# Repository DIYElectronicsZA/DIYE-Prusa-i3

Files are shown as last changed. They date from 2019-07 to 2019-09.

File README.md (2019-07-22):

# DIYE-Prusa-i3
DIYElectronics version of the Prusa i3 https://diyelectronics.co.za

Based on the Original Prusa i3, the DIYElectronics Prusa i3 is a 3D printer project maintained by DIYElectronics.co.za
Originates in RepRap project.

This repository contains files and STLs of the printed parts.

**Links**

 * DIYElectronics website : http://diyelectronics.co.za
 * Product page : https://www.diyelectronics.co.za/store/printers/903-diyelectronics-prusa-i3-premium-kit.html
 * Build manual : https://www.diyelectronics.co.za/wiki/#3DPrinters/DIYPrinters/builddocprem/
 * Firmware : https://www.diyelectronics.co.za/firmware/

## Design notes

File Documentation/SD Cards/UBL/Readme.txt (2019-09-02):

On this SD Card, you will find "UBL.gcode"
This gcode script is used to initiate a UBL sequence.
You should run this script every time you:
	- Move / transport the printer
	- Remove / re-level the bed
	- If your bed has become warped over time

Read more about UBL at http://marlinfw.org/docs/features/unified_bed_leveling.html

If you have any queries, don't hesitate to contact Support@DIYElectronics.co.za

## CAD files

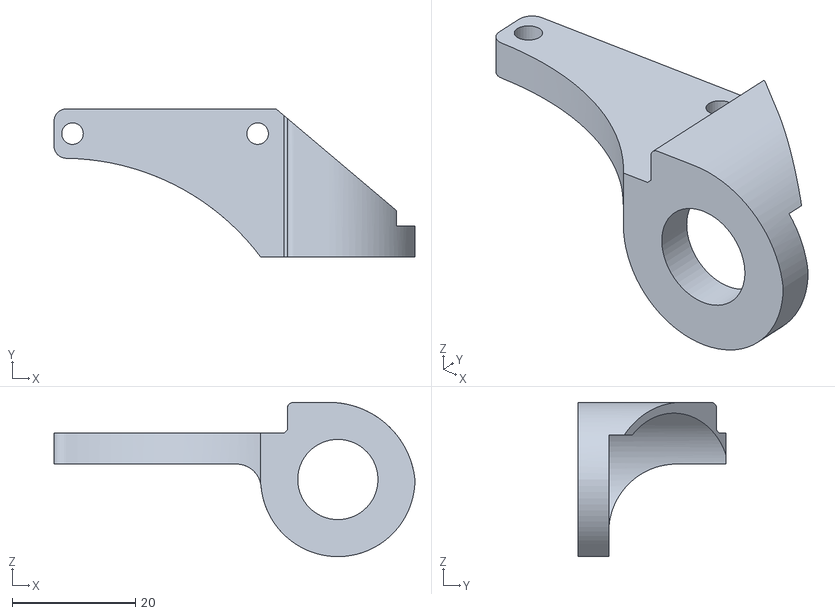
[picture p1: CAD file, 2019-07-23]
Printed Parts/Auto Level Kit/Autolevelmount.stl
58.5 x 24.0 x 25.0

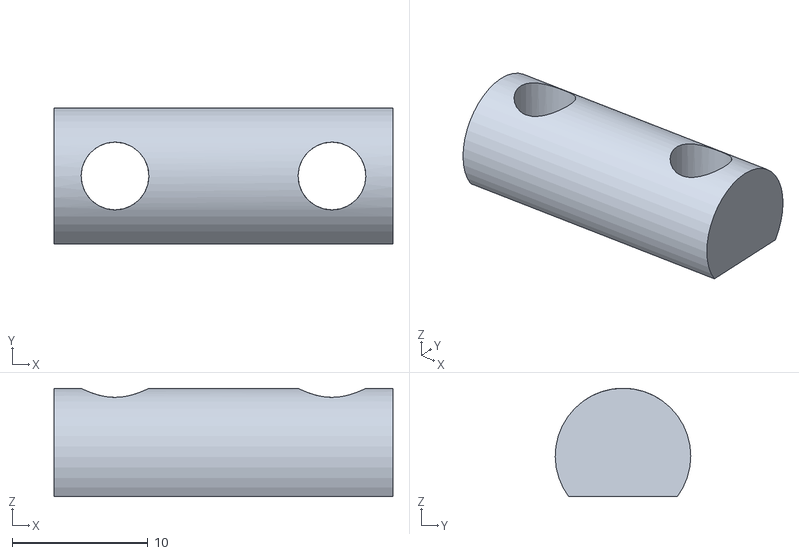
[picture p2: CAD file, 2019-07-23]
Printed Parts/Charlstruder/Birdnose Shaft/Birdnose shaft.stl
25.0 x 10.00 x 8.00

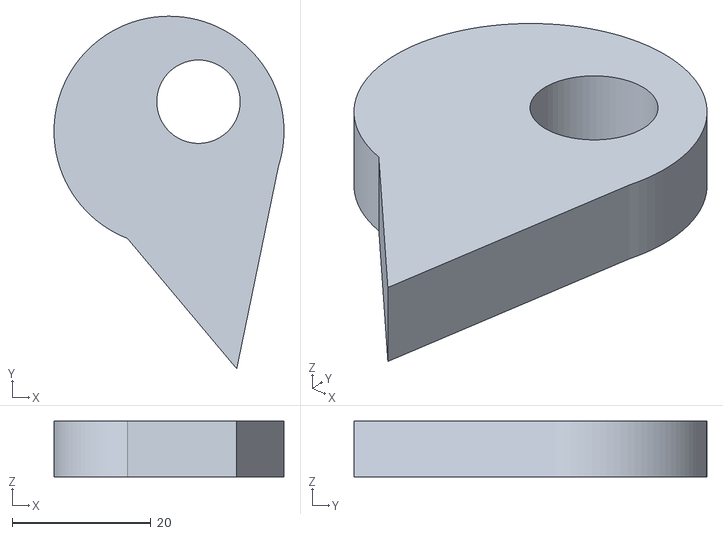
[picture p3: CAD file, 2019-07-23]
Printed Parts/Charlstruder/Birdnose/Birdnose.stl
33.1 x 50.7 x 8.00

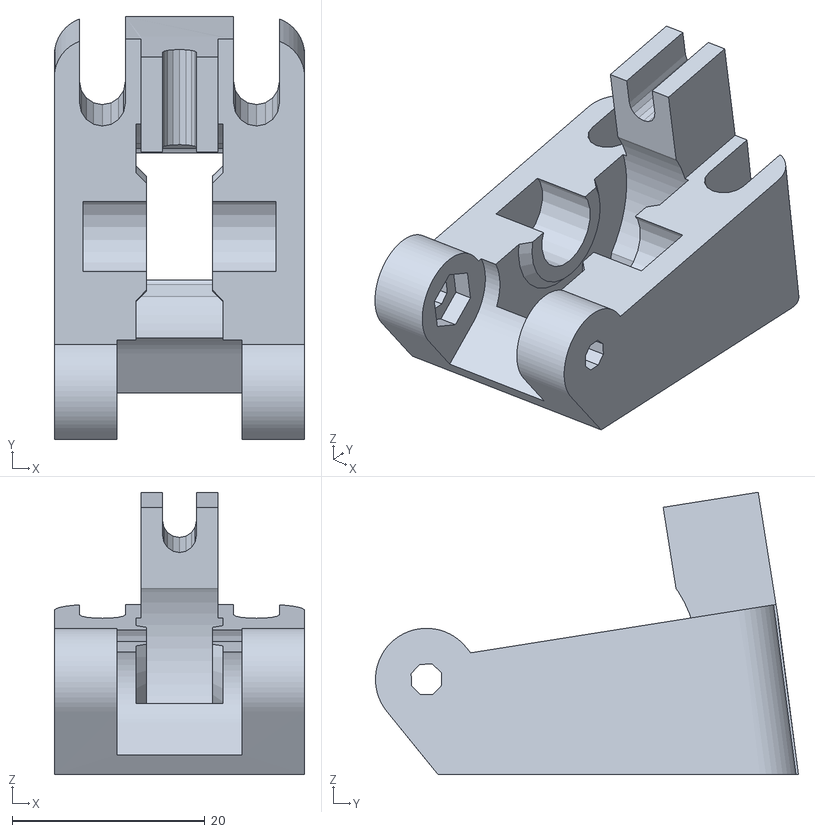
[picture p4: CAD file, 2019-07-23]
Printed Parts/Charlstruder/Charlstruder Birdnose Guidler/Birdnose Guidler.stl
26.0 x 43.9 x 29.3

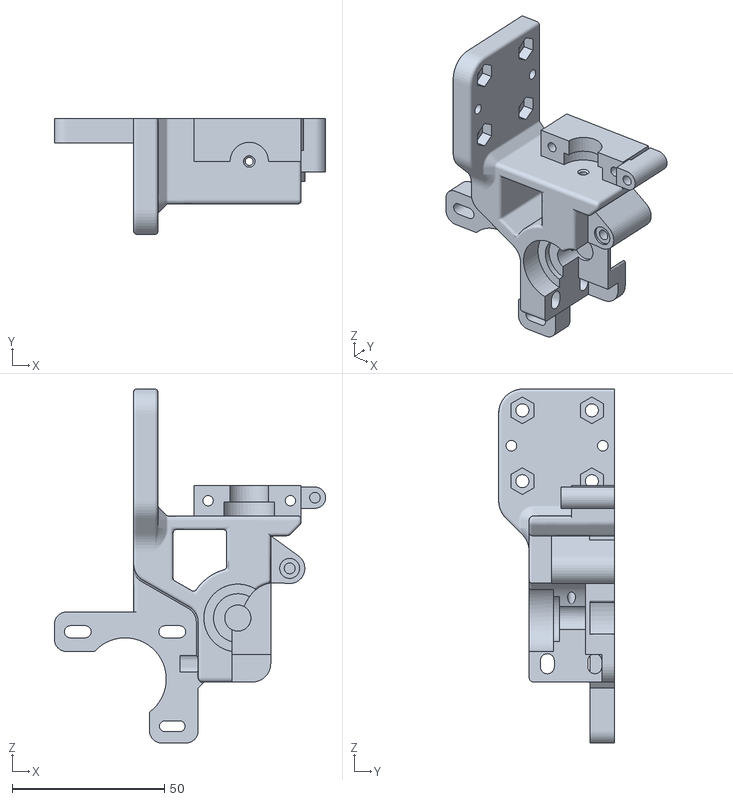
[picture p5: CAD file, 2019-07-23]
Printed Parts/Charlstruder/CharlStruder Body/Charlstruder_E3D_1.75mm_v1.1.stl
89.0 x 38.0 x 116.2

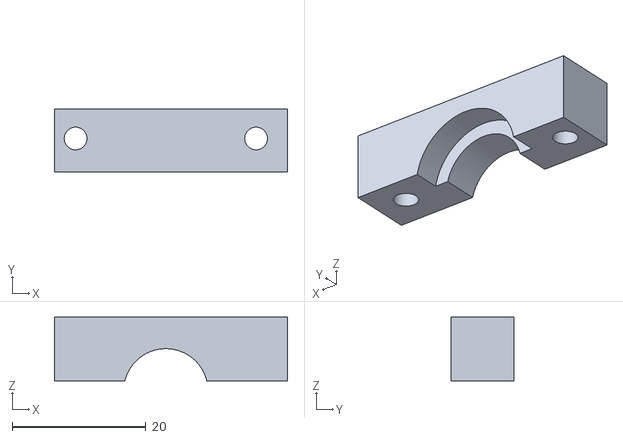
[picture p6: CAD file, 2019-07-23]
Printed Parts/Charlstruder/Charlstruder Collar/Hotend Collar.stl
34.9 x 9.40 x 9.50

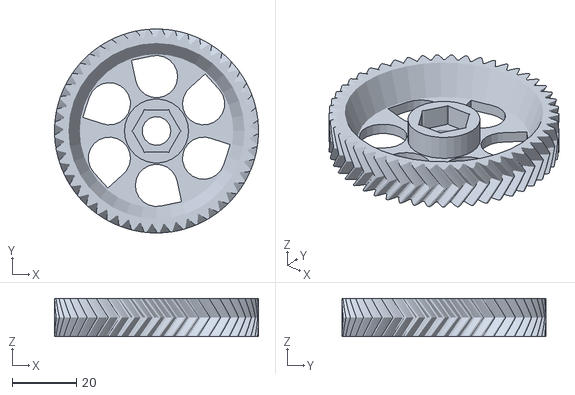
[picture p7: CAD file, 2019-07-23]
Printed Parts/Charlstruder/Charlstruder Gears/13mm Drive Gear/Charlstruder Gears.stl
63.7 x 63.7 x 12.0

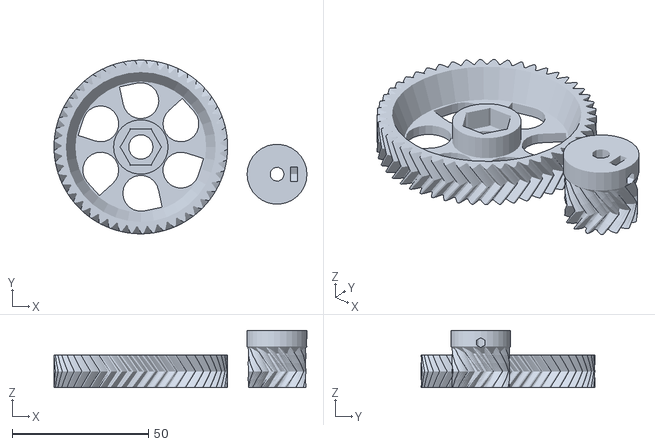
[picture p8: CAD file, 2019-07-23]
Printed Parts/Charlstruder/Charlstruder Gears/Pinion Gear/Charlstruder Gears.stl
92.9 x 63.7 x 21.0

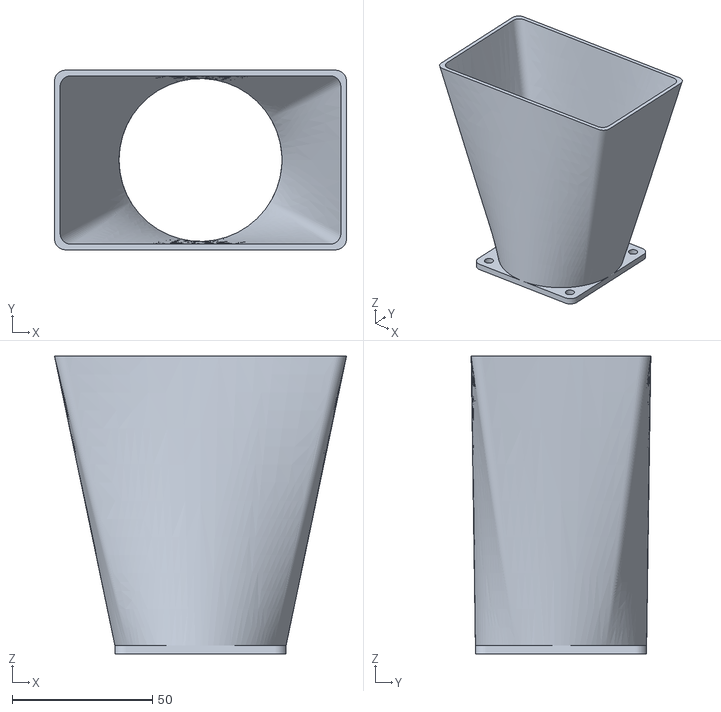
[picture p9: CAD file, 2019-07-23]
Printed Parts/DIY Enclosure/60mm Fan Duct/RampsFanExtenderShroud.STL
104.0 x 64.0 x 106.0

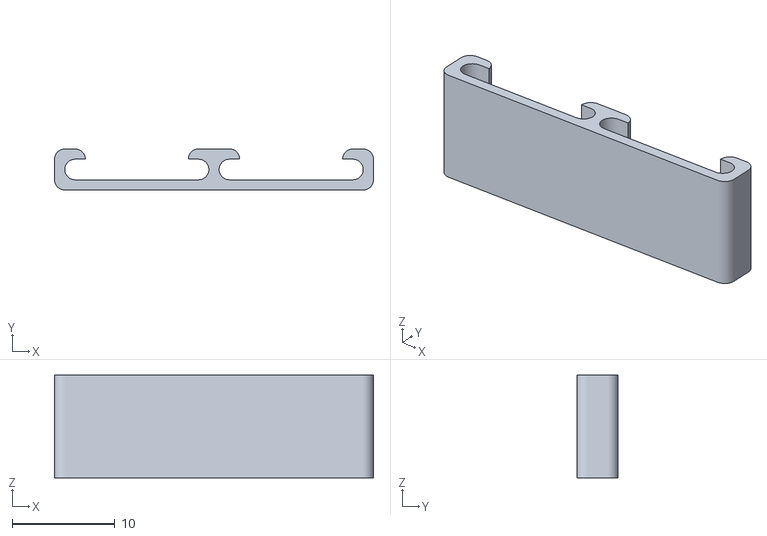
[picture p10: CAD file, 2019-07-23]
Printed Parts/DIY Enclosure/Cable Clip/Cable Clip.STL
31.0 x 4.00 x 10.0

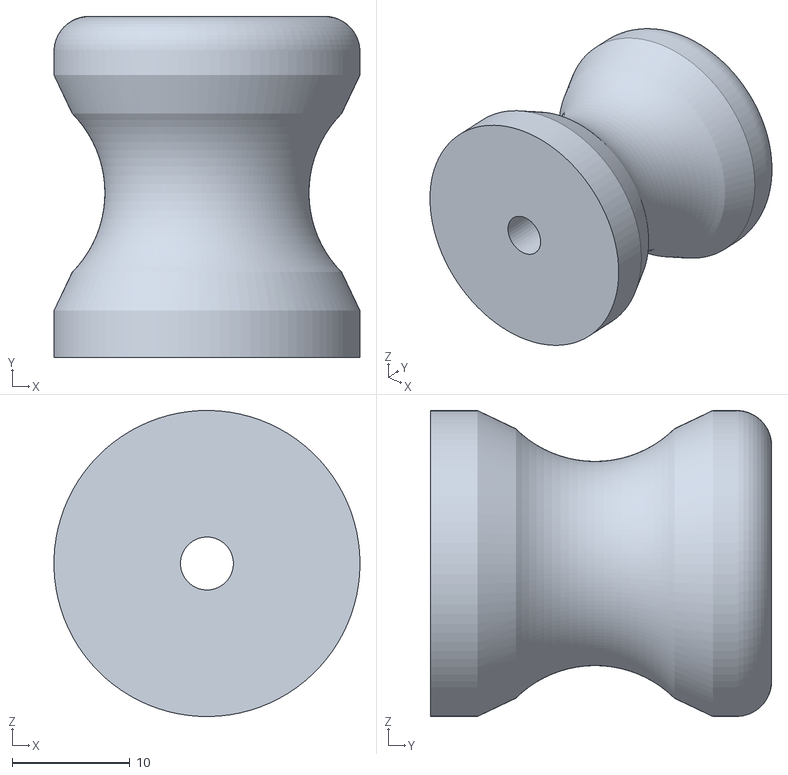
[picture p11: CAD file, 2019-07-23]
Printed Parts/DIY Enclosure/Door Knob/knob.stl
26.0 x 29.0 x 26.0

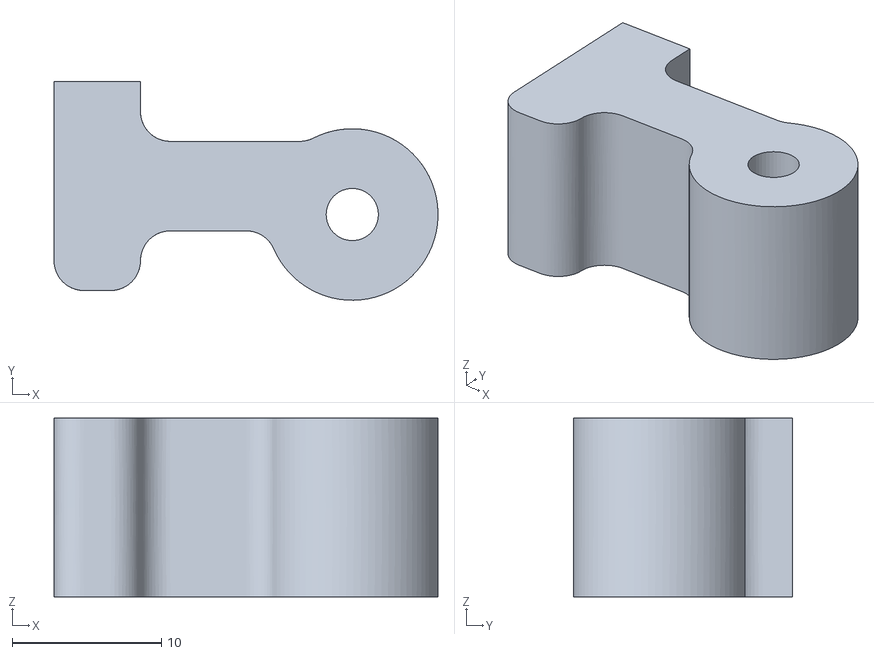
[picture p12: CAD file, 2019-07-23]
Printed Parts/DIY Enclosure/Door Magnet Mounts/frame mag latch.stl
25.7 x 14.7 x 12.0

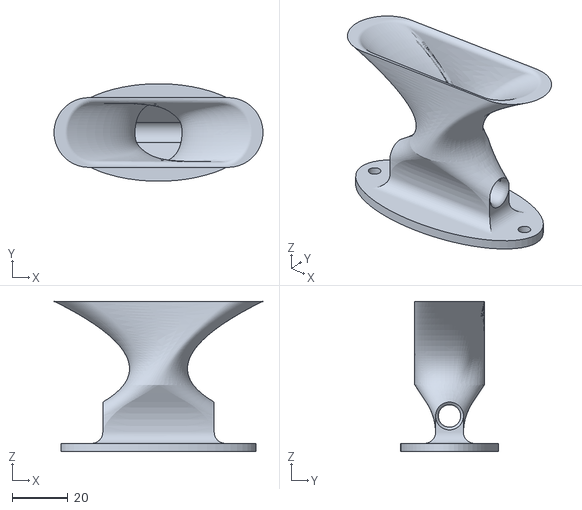
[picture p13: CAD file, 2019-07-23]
Printed Parts/DIY Enclosure/Filament Guides/Filament Guide 2.STL
75.0 x 35.0 x 54.0

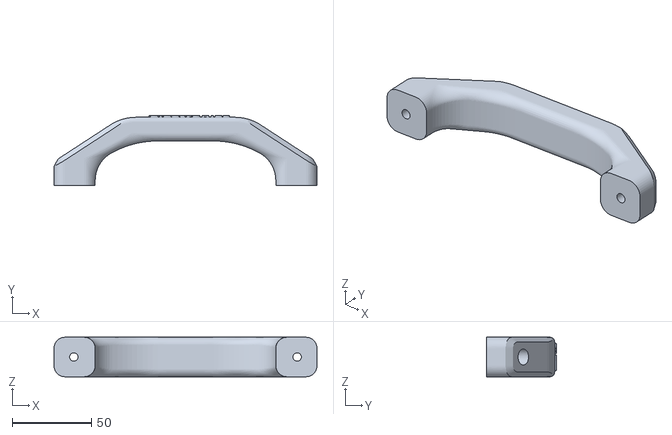
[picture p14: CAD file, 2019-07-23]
Printed Parts/DIY Enclosure/Handle/HandleV2.stl
166.0 x 44.0 x 25.0

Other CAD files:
Printed Parts/Charlstruder/Charlstruder Gears/14mm Drive Gear/Charlstruder Gear 14mm.stl
Printed Parts/DIY Enclosure/Hinge/hinge1.stl
Printed Parts/DIY Enclosure/Printer Mount/Prusa Mount.stl
Printed Parts/DIY Enclosure/Spool Holder/Spool Holder.stl
Printed Parts/DIY Enclosure/Door Magnet Mounts/door mag latch.stl
Printed Parts/DIY Enclosure/Door Magnet Mounts/frame mag latch_MIR.stl
Printed Parts/DIY Enclosure/Filament Guides/Filament Guide 1.STL
Printed Parts/DIY Enclosure/Hinge/hinge2.stl
Printed Parts/DIY Enclosure/Thumb Screw/M3-rosette-thumb-screw.stl
Printed Parts/DIY i3 BASE/608 Bearing Mounts x 8/608 Bearing Mount_4/608 Bearing Mount x8.stl
Printed Parts/DIY i3 BASE/608 Bearing Mounts x 8/608 Bearing Mount_5/608 Bearing Mount x8.stl
Printed Parts/DIY i3 BASE/Endswitches/Endstop X.stl
Printed Parts/DIY i3 BASE/Endswitches/Endstop Y.stl
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

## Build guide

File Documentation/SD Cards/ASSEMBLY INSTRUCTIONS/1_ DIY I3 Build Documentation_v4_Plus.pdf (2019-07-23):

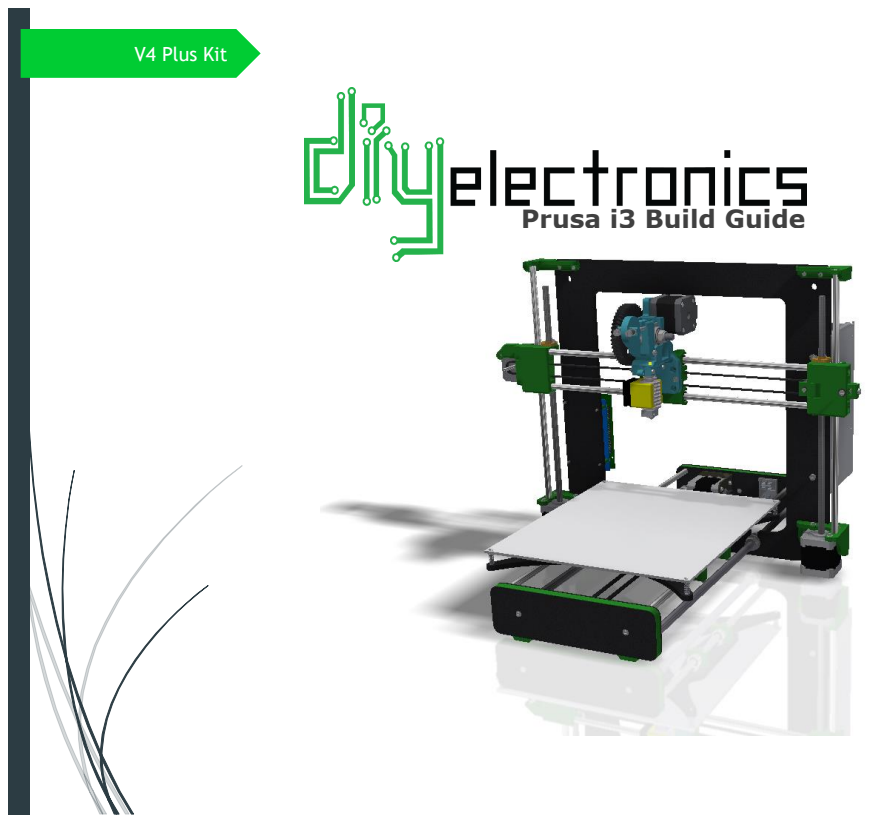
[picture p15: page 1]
V4 Plus Kit

Prusa i3 Build Guide

1

Hi! Congratulations on your purchase of the DIYElectronics.co.za Prusa I3 kit, the best South African 3D Printer Kit! Hopefully this should serve as complete guide to get your printer setup and printing!

This guide will start with a step by step mechanical assembly, and then onto electronic wiring and calibration.

### Please take note of the following points before continuing with this this guide

!!!

- This is a new and upgraded build guide so in the case of errors or mistakes please kindly let us know at support@diyelectronics.co.za. We want to constantly upgrade this for to make this build as easy and seamless as possible. Don’t be shy. But make sure you read everything before you email ;)
- Due to the nature of Rapid Prototype 3D printed parts, cleaning-up, drilling, filing, cutting of the plastic parts may be necessary. This is important. If you want your build to go smoothly you MUST read all of the *Notes and *Tips along the way. Most of the holes need to be drilled out for precision. You don’t want to force anything and break your plastic components.
- Be patient and thorough. Take time to make sure you put things together properly. Believe us when we say it will save you LOTS of time if you do it right first.

2

# Contents

3

# [1] Y-Axis

4

Front gasket | 1 | y -bed carriage | 1 | 624f flanged bearing | 2
Rear gasket | 1 | y -axis motor mount | 1 | LM8UU linear bearing | 4
M10x480 threaded rod | 2 | Bearing holder | 8 | Nema 17 stepper motor | 1
M8x475 smooth linear rod | 2 | y -belt tensioner | 1 | M10 Nut | 12
front outer plate | 1 | y -belt holder | 1 | M10 Washer | 8
Front inner plate | 1 | IEC mains and switch | 1 | M3 machine screws, washers, nuts
Back inner plate | 1 | USB extender | 1 | M4 machine screws, washers, nuts
Back outer plate | 1 | GT2 20tooth pulley | 1

5

### [1.1] Y Carriage – Sub Assembly:

Parts needed:

- 1x aluminum carriage
- 2x M8x475 mm smooth stainless steel rod
- 4x LM8UU linear bearings
- 8x printed bearing holders
- 1x printed y-belt holder
- 2x M3x10 mm ch screws
- 8x M3x25 mm ch screws
- 10x M3 washers

Drill out all the holes of the printed parts with a 3mm drill bit.

Slide two LM8UU linear bearings onto each smooth 475 mm rod.

Fix the printed Y-belt to the carriage with the use of two M3x10 machine screws

Line the bearings, rods, and printed bearing holders with the holes in the Y-carriage as shown in the top diagram.

Fasten it all down with eight M3x25 screws (don’t forget the washers)

NOTE* Make sure the linear rods slide smoothly within the bearings. Overtightening the bearing holders will restrict movement.

6

### [1.2] Y-Bed Undercarriage Sub-assembly

Parts needed:

- 2x M10x480 threaded rod
- 8x M10 nuts
- 8x M10 washers

Thread M10 nuts and washers onto the two M10 threaded rods as seen in the image above.

Make sure that the distance between the outer washer on one side and the nearest inner washer is 155 mm. This is important.

7

### [1.3] Y-Axis assembly

Parts needed:

- Y Carriage Sub-Assembly
- Y Bed Undercarriage sub-assembly
- Inner front plate
- Inner back plate
- Front printed gasket
- Back printed gasket
- 4x M10 nuts

**Drill out the holes of the printed gaskets. You will need a size 3, 8 and 10 size drill bit**

Assemble the Y-Axis by sliding the plates
and gaskets onto the ends of the smooth
and threaded rods. The M8 smooth rods
should fit snugly into the printed gasket holes.

There should be exactly enough threaded rod protruding from the printed gaskets to fit M10 nuts onto.

Tighten these four M10 nuts with a size 17 spanner.

NOTE: Make sure that you tighten the 4 M10 nuts on a flat surface to ensure a flat Y-Axis assembly.

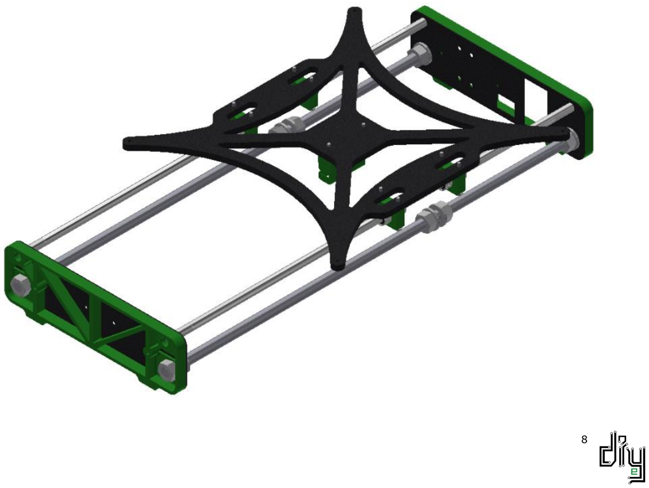
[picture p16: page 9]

8

9

### [1.4] Y-Belt Idler pulley sub-assembly

Parts needed:

- 1x printed Y-belt idler
- 2x 624 flanged bearings
- 1x M4x25 machine screw
- 2x M4 washers
- 1x M4 nyloc nut
- 2x M3x20 machine screws
- 2x M3 washers
- 2x M3 nuts

First fasten the printed Y-Belt idler bracket to the front inner end plate. Use M3x20 machine screws and fasten into M3 nuts which are to be held captive in the printed bracket.

Feed an M4x25 screw though the bracket and TWO 624 flanged bearings butted up against each other. Don’t forget about the washers on either side.

Tighten with an M4 nyloc nut. You want the bearings to rotate smoothly so don’t overtighten.

10

### [1.5] Y-motor mount Sub-assembly

Parts needed:

- 1x motor mount
- 4x M4x10 machine screws
- 8x M4 washers
- 4x M4 nuts

Fix the Y-motor mount to the rear inner end plate using 4x M4x10 screws, washers, and nuts as shown in the image. Make sure that the mount is straight and parallel to the top of the end plate.

NOTE* The distance from the edge of the motor mount to the edge of the end plate needs to be about 40 mm

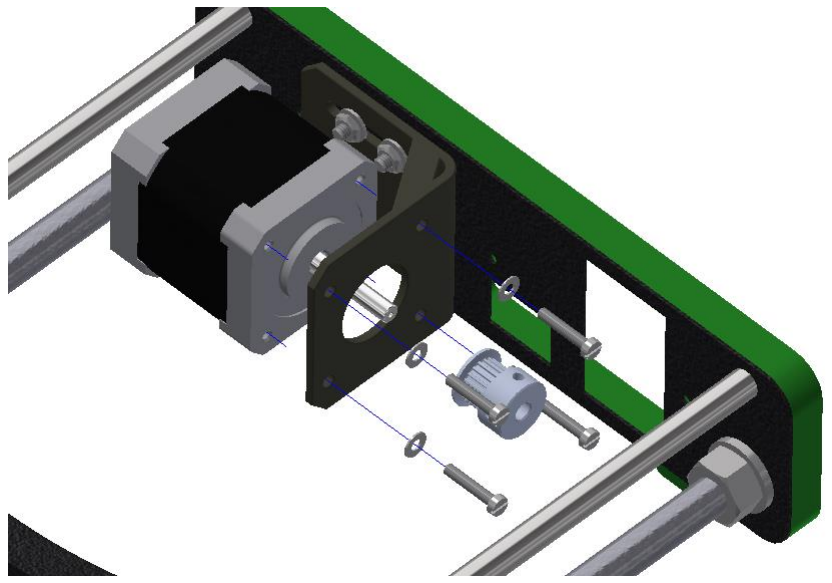
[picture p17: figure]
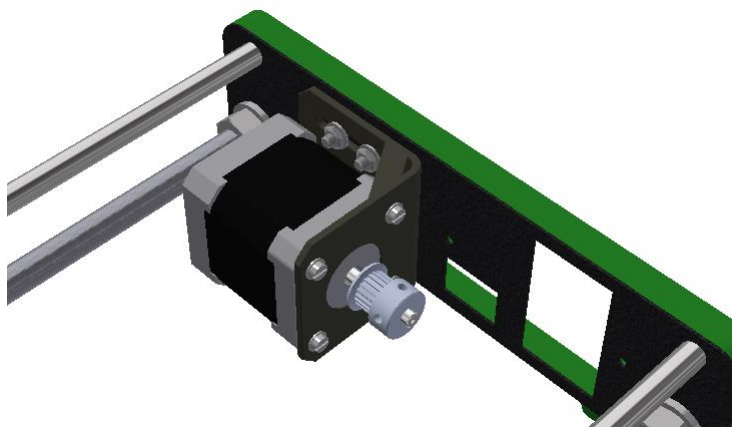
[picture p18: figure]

11

### [1.6] Y Motor sub-assembly

Parts needed:

- 1x Nema 17 stepper motor
- 1x GT2 20t pulley (with 2 M3 grub screws)
- 4x M3x8 machine screws
- 4x M3 washers

Fix the Y axis Nema 17 stepper motor to the motor mount using four M3x10 machine screws with washers as seen in the picture above. Tighten well, but not enough to strip the thread of the stepper motor.

Then slide the GT 2 pulley onto the stepper motor shaft. Position the pulley so that the center of the teeth line up with the center of the idler bearing on the other side of the axis (see the next section)

12

### [1.7] Y-Axis timing belt

Parts needed:

- 1x timing belt
- 1x spring tensioner
- 4x cable ties

Make sure that the centre of the GT2 pulley, centre of the Y-Belt holder, and the centre of the Y-belt idler bearing are all in line with each other. If they are not, you will need to loosen the pulley grub screws and position the pulley (possibly flip it around). If this still doesn’t work you will need to loosen the Y-motor mount M4 screws and reposition the mount.

Next you have to flip the entire Y-axis around and attach the timing belt.

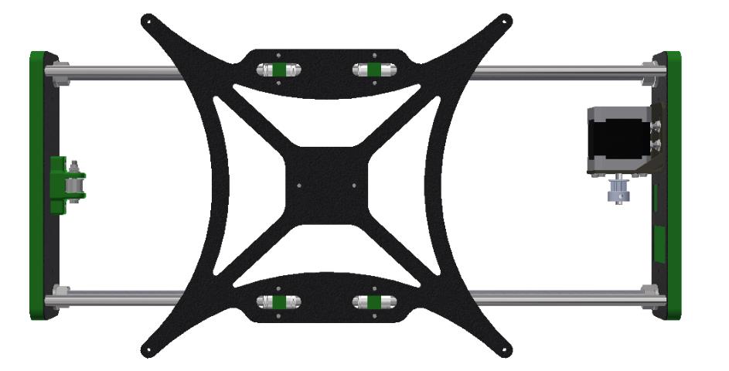
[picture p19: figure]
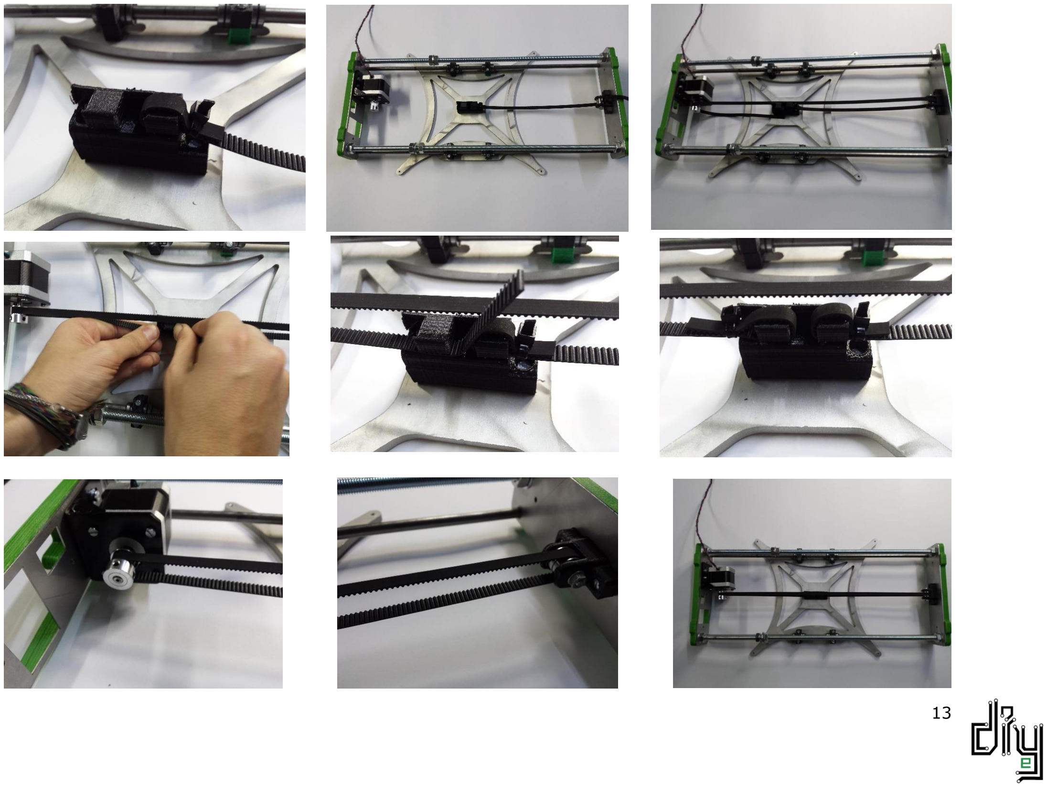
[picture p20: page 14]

13

14

### [1.8] Outer end plates

**NOTE** The cutout for the IEC connecter is no longer present on the rear outer plate. The IEC connecter now is included in the PSU kit

Parts needed:

- 1x rear outer end plate
- 1x USB male to USB female adapter
- 2x M3x10 machine screws
- 2x M3 washers
- 5x M3x20 machine screws
- 10x M3 washers
- 5x M3 nuts

Fix the female end of the USB adapter to the rear outer end plate as seen in the images.

15

Next up is fixing the outer end plates to the front and rear gaskets. Do this by inserting three M3x20 screws with washers through the read outer end plate – through the gasket and rear inner end plate. Place washers on the protruding ends of the screws and tighten with M3 nuts.

16

17

Well done! Your printer’s Y-Axis assembly is now complete :D

18

# [2] X-Axis

19

Parts needed:

420mm smooth linear rods (x-axis) | 2x | LM8UU linear bearings | 7x
320mm smooth linear rods (z-axis) | 2x | Nema 17 stepper motor | 1x
Printed x-end | 1x | GT2 pulley (with grub screws) | 1x
Printed x-end motor | 1x | M3x10mm machine screw | 3x
Printed x-axis carriage | 1x | M4x25 machine screw | 1x
Y-axis tensioner | 1x | M4x20 machine screw | 2x
F624 idler bearing | 2x | M4 washer | 3x
M4 Nyloc nut | 1x | M4 nut | 2x

20

STEP 1
- Insert two M8x420 linear rods into the printed x-end motor bracket

Note: will probably need to drill out the holes on both x-end parts with an 8 mm drill bit.

STEP 2
- Slide on two LM8UU linear bearings onto the bottom rod and one on the top
- Snap the printed x-axis carriage onto the bearings.
- Make sure that the bearings line up perfectly with their mounting cavities!
STEP 3
- Press fit the other printed x-end part onto the two linear rods.
- The distance between the two inner faces of the x-end parts (or the length of exposed linear rod) needs to be 347 mm.

21

STEP 4
- Slide two LM8UU linear bearings onto each M8x320mm z-axis linear rods
- Press fit the bearings (with rods inserted) into their cavity slots. Once again, it is VERY important that the bearings seat perfectly into their slots.
- Check that the x-axis runs smoothly up and down the bearings. If there is excess friction this would indicate improper seating or alignment of the bearings

NOTE: at this point you need to drill out the 10mm and 3mm holes in each x-end. This is to make your life easier later.

22

STEP 5
- Slide the 20tooth GT2 pulley onto the shaft of the Nema 17.
- Tighten the two grubscrews with a suitable allen key – thereby fixing the pulley to the motor shaft
STEP 6
- Fix the Nema 17 stepper motor to the printed x-end bracket using three M3x10 machine screws
- Make sure that the center of the pulley’s teeth are aligned with the centre of the slot of the printed x-end

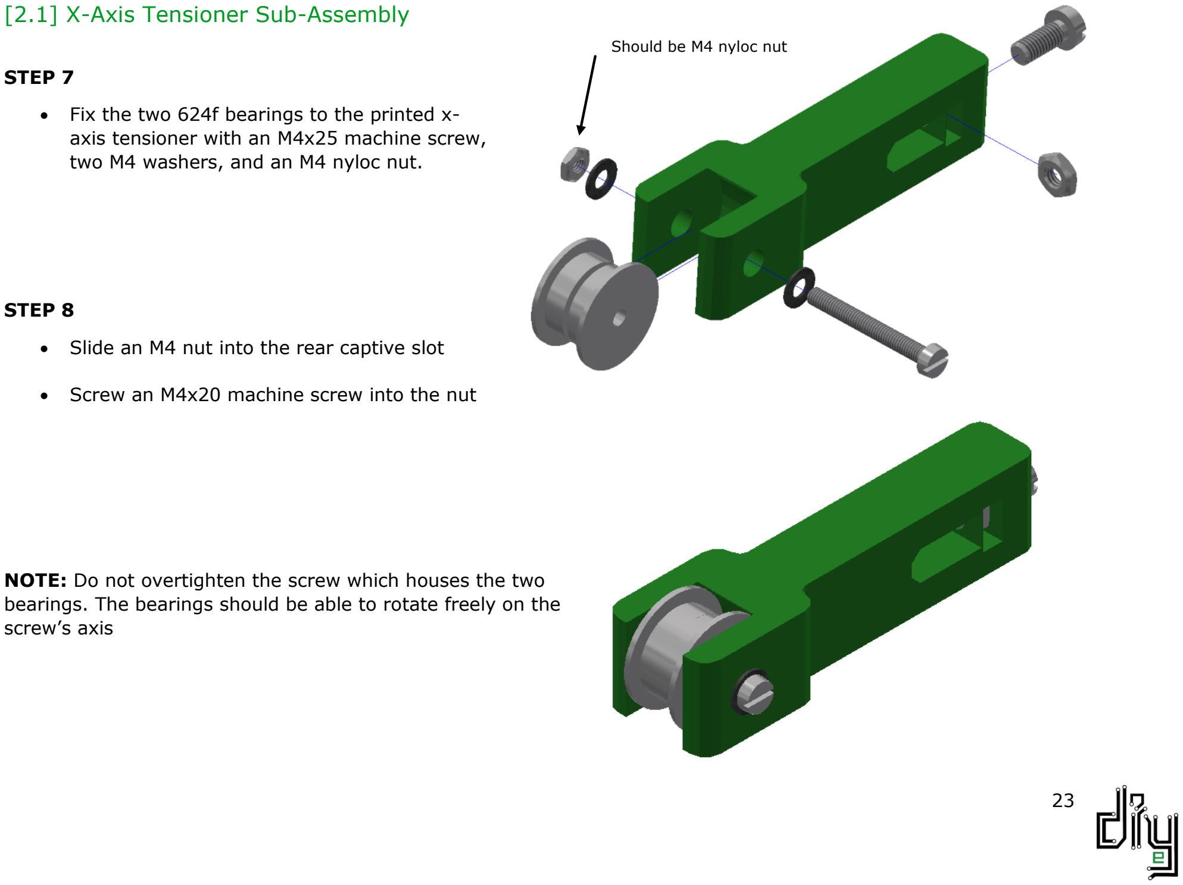
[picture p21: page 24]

23

### [2.1] X-Axis Tensioner Sub-Assembly

STEP 7
- Fix the two 624f bearings to the printed x-axis tensioner with an M4x25 machine screw, two M4 washers, and an M4 nyloc nut.
STEP 8
- Slide an M4 nut into the rear captive slot
- Screw an M4x20 machine screw into the nut

NOTE: Do not overtighten the screw which houses the two bearings. The bearings should be able to rotate freely on the screw’s axis

Should be M4 nyloc nut

24

STEP 9
- Slide the x-axis tensioner sub-assembly though the printed right side x-end

NOTE** This can sometimes be a tight fit. You don’t want to break the x-end so sanding or filing of the sides of the tensioner may be required.

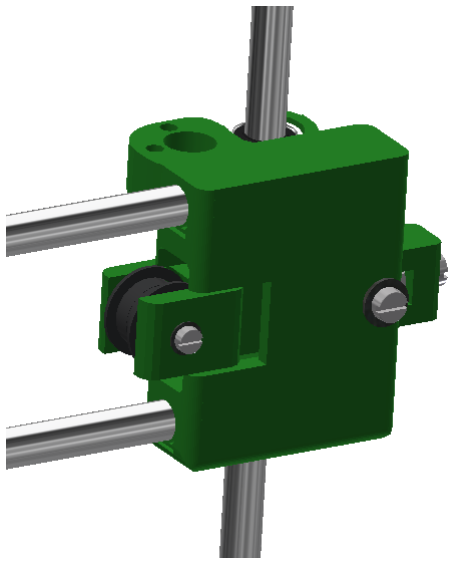
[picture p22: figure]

STEP 10
- Once the tensioner is in, insert an M4x20 machine screw with washer and nut through the tensioner’s slot (indicated by the red arrow). This screw acts as a backstop which the M4 screw in the rear of the tensioner sits against.

TIP: Make sure to leave the rear tensioning screw as unscrewed as possible (the image is incorrect and shows it fully screwed in and tensioned). You only want to tension it once you have installed the timing belt.

25

[3] Z

# –Axis

Parts needed:

Aluminium 6mm frame | 1x
Nema 17 stepper motor | 2x
Printed z -axis bottom left corner | 1x
Printed z -axis bottom right corner | 1x
M3x10 machine screw | 12x
M3 washer | 6x

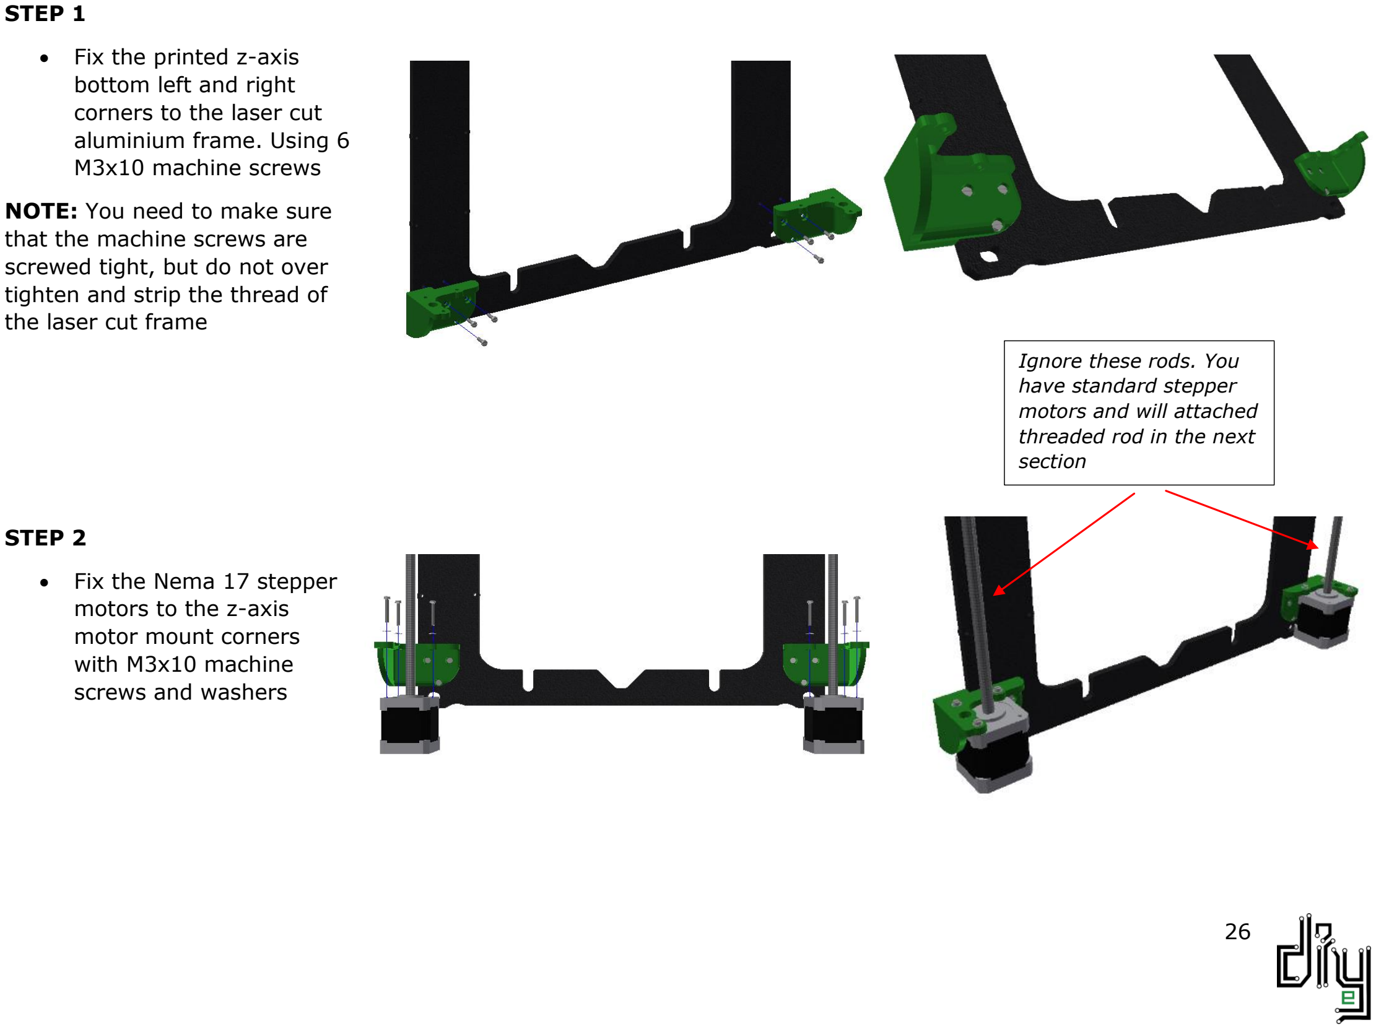
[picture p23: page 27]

26

STEP 1
- Fix the printed z-axis
bottom left and right
corners to the laser cut
aluminium frame. Using 6
M3x10 machine screws

NOTE: You need to make sure that the machine screws are screwed tight, but do not over tighten and strip the thread of the laser cut frame

STEP 2
- Fix the Nema 17 stepper
motors to the z-axis
motor mount corners
with M3x10 machine
screws and washers

Ignore these rods. You
have standard stepper
motors and will attached
threaded rod in the next
section

27

# [4] XZ-axis Mate

Z-axis subassembly (standard Z motors without leadscrews) | 1x

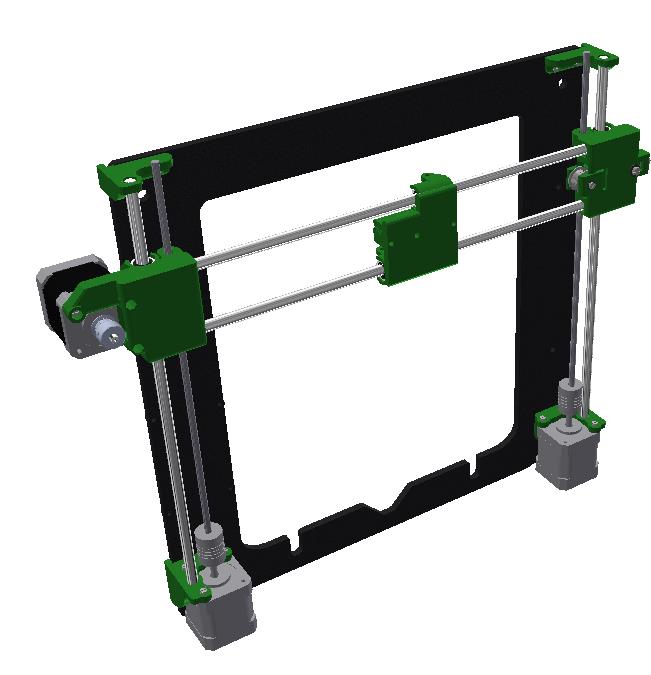
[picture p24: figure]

X-axis subassembly (standard x-ends) | 1x
Printed z-axis top left corner | 1x
Printed z-axis top right corner | 1x
M5 nut | 2x
M3x10 machine screw | 4x
Aluminium Couplers | 2x
M5 x 300mm threaded rod | 2x

28

STEP 1
- Get your X-axis assembly ready and press fit the two M8x320 smooth rods into the bottom two printed Z-corners (red arrows)
- You need to make sure that the distance between the x-ends 85 mm (orange arrow). And that the M8 smooth rods are parallel to the frame’s edge.

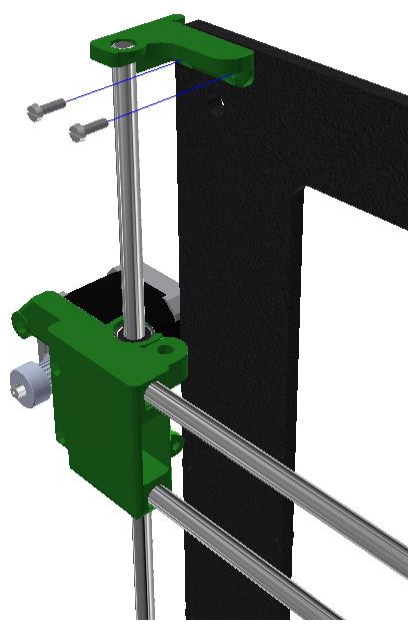
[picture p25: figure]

STEP 2
- Drill out the top left and right z-axis corners. Press fit the left top z corner on top of the left 320mm smooth rod.
- Fix the left side corner to the aluminium frame with two M3x10 machine screws

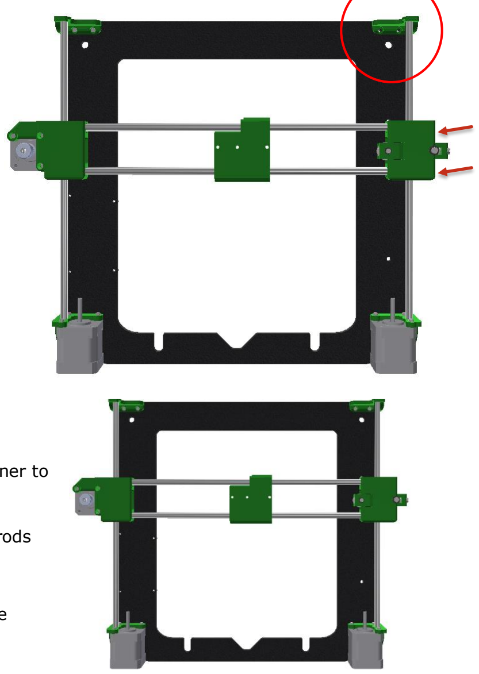
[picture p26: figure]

29

STEP 3
- Press fit the top right z corner onto the M8 smooth rod
- Use a mallet or hammer to lightly tap the x-end (indicated by red arrows) until the top right z-axis corner lines up with the aluminium frame holes.
STEP 4
- When you are happy with the alignment, fit the top right corner to the frame using two M3x10 machine screws.
- The X-Axis should traverse up and down the Z-axis smooth rods without any binding.

NOTE! It is very important to ensure that there is NO bowing of the smooth rods. This will cause problems with binding

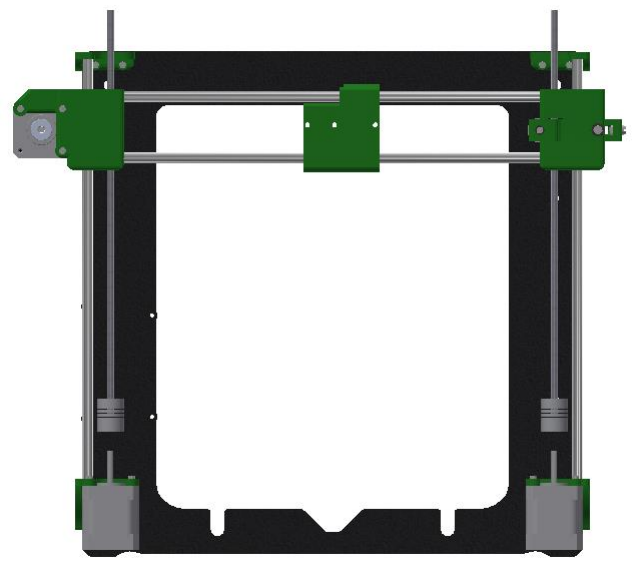
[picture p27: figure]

30

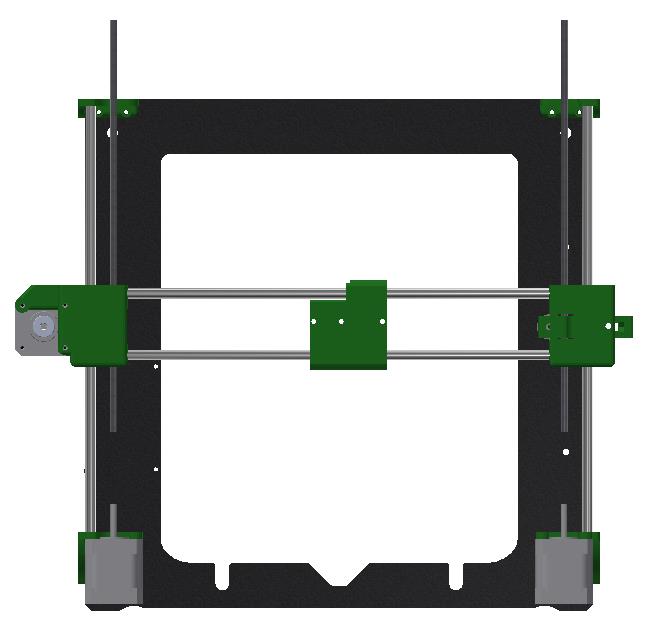
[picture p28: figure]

STEP 5
- Thread the two M5x300 thread rod shafts into the M5 nuts already inserted into the
two x-ends (you want to use machine oil to lube this when you are done).
- Fix the two aluminium couplers to the bottom of each of these rods. Tighten the two upper grub screws on each flex coupler using an allen key.
- Lower the x-axis down, thereby coupling the threaded rod and stepper motor shafts. Make sure that the two rods are perpendicular and everything is true. Tighten the bottom two grub screws onto the stepper motor shafts.

*TIP* There should be a gap between the 300mm threaded rod and the stepper motor shaft inside the coupler. These should not be up against each other.

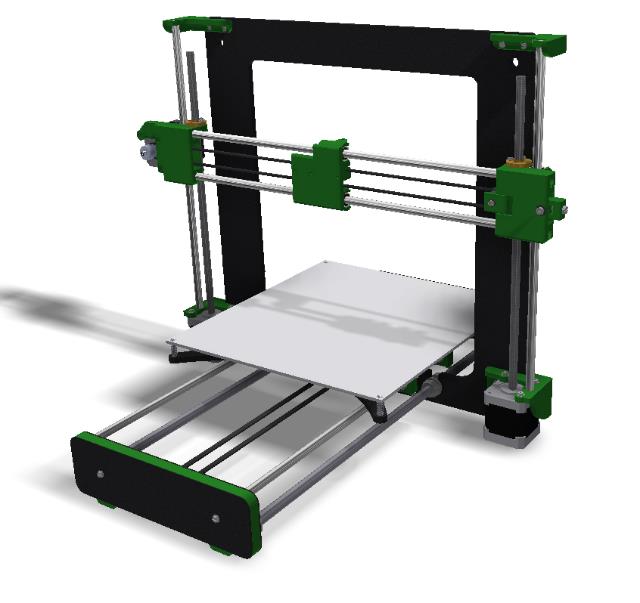
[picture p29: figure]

31

# [5] YZ – axis Mate

ZX axis subassembly | 1x
Y axis subassembly | 1x
Aluminium Bed | 1x
Kapton heater pad and thermistor (Attached to above Aluminium Bed) | 1x
Bed springs | 4x
M3x25 countersunk machine screws | 4x

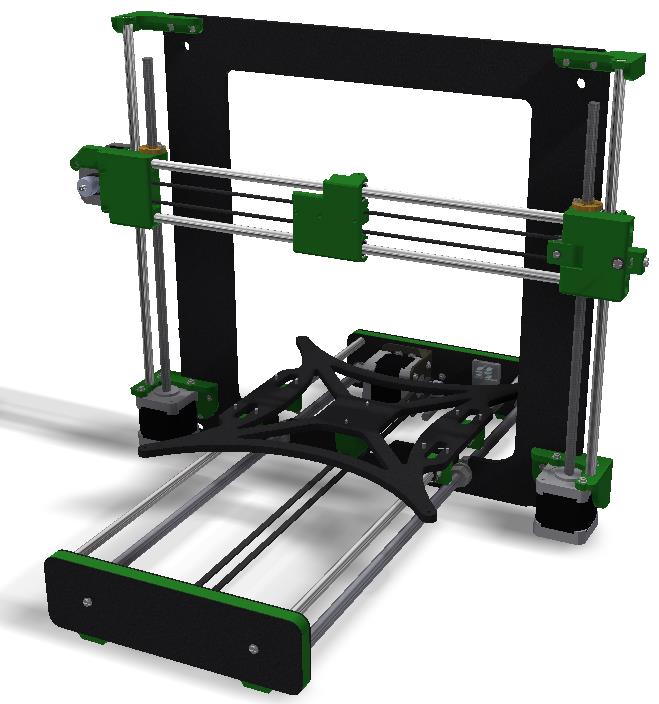
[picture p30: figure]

32

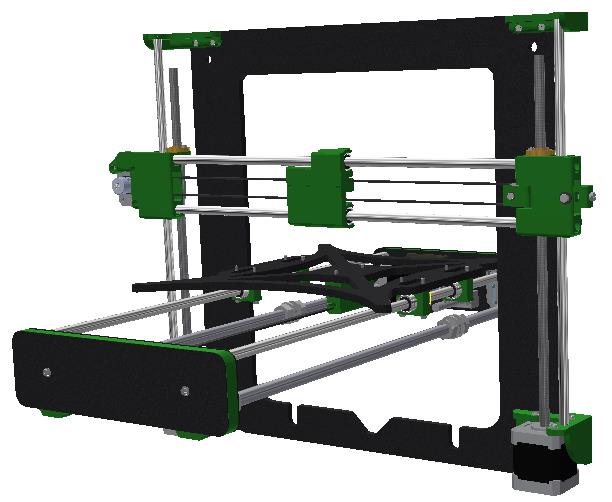
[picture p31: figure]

STEP 1
- Slot the Y-axis assembly down into the slots of the aluminium frame
- Keep in mind the 155mm clearance distance mentioned in the first section
STEP 2
- Tighten the M10 nuts with a size 17 spanner
- Make sure that the feet of the aluminium frame and the printed gaskets are level!
STEP 3
- Install the timing belt similarly to how it was done on the Y-axis. See example picture on the right. Secure ends by x-carriage with cable ties. (You will need to break away the supports on the x-carriage in order to insert the belt)

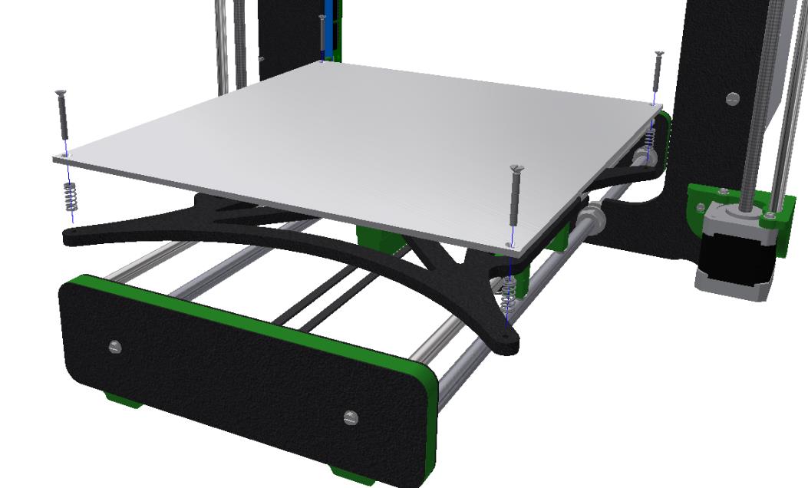
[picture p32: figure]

33

STEP 5
- Using four M3x25 countersunk screws, fix the print bed to the y-carriage. Make sure that there are springs sandwiched between the bed and the carriage.
- Ensure that the heater pad wires under the aluminium bed fact the back of the printer

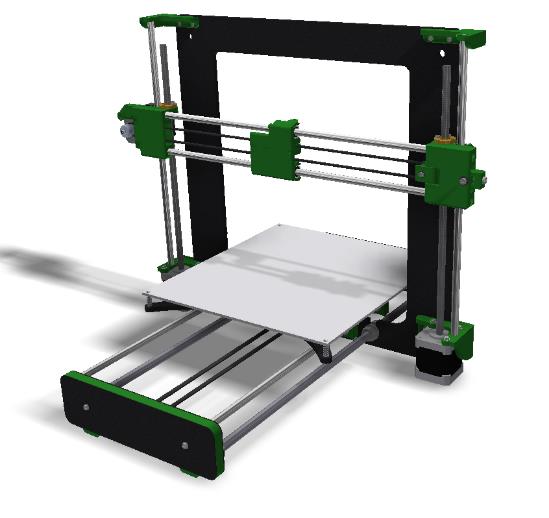
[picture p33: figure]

34

# [6] Electronics and Extruder Assembly

Arduino Mega | 1x
Ramps 1.4 | 1x
12V power supply (With cover containing power connector and switch) | 1x
Printed standoff | 4x
M4x10 machine screw | 2x
M3x20 | 4x

Auto Bed Levelling Kit

Extruder and hotend subassembly

35

STEP 1
- You will receive both your Arduino Mega and Ramps 1.4 control board assembled and ‘mated’ together. Evenly apply force to the edges of both boards to pry the two apart
- Fix the Arduino mega to the frame using four M3x20 machine screws and standoffs between the frame and the bottom of the Arduino
- Once it is secure, press the Ramps 1.4 shield back into place (try not bend any pins and make sure that all of the pins are inserted fully)
STEP 2
- Secure the 12V power supply to the frame using two M4x10 machine screws.

The Power supply comes with a protective cover attached. This cover also houses the IEC power socket and fused on/off switch!

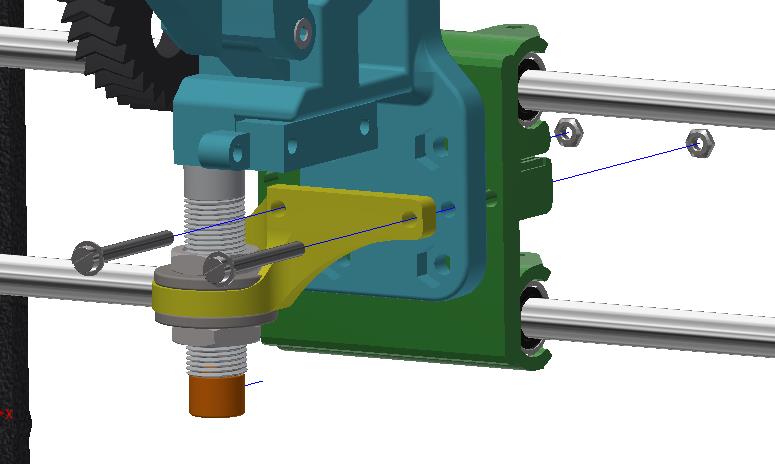
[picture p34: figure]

36

STEP 3 - *REFER TO CHARLSTRUDER INSTRUCTIONS ON HOW TO ASSEMBLE THE EXTRUDER*
STEP 4 – Mounting Extruder and Auto Bed Level Probe Mount
- Fix the completed extruder and Auto Bed Levelling Probe mount the to the x-axis carriage using two M3x35 machine screws, M3 washers, and M3 nuts.

Tip: You might need to remove the hotend from the clamp temporarily if it is in the way and you can’t get your screwdriver on either side of the hotend fins.

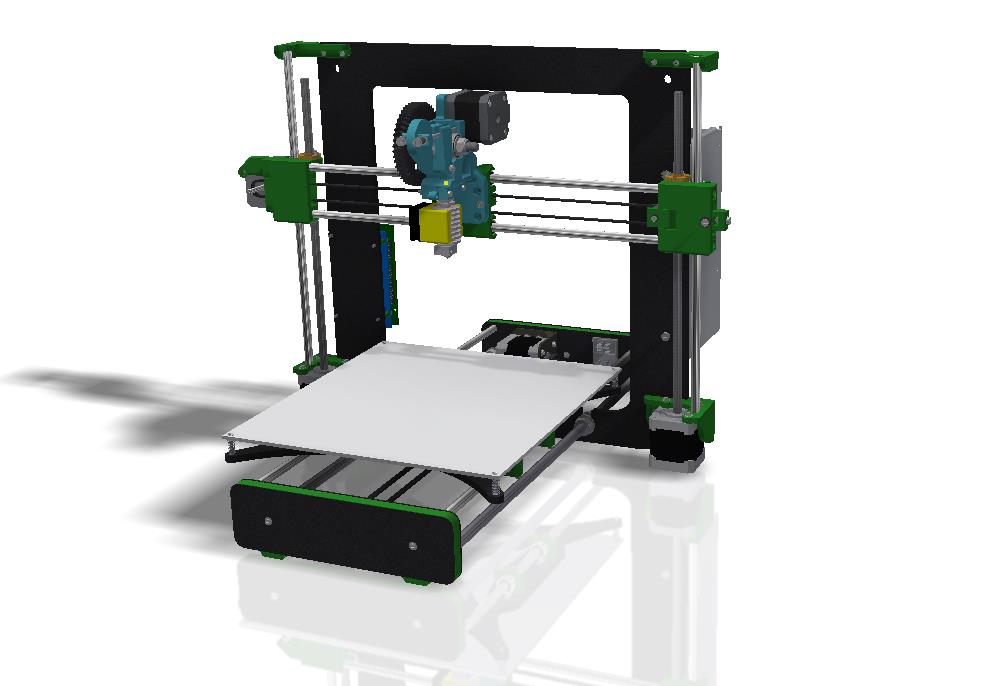
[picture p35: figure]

Your printer should look like this. Nearly there :D !!

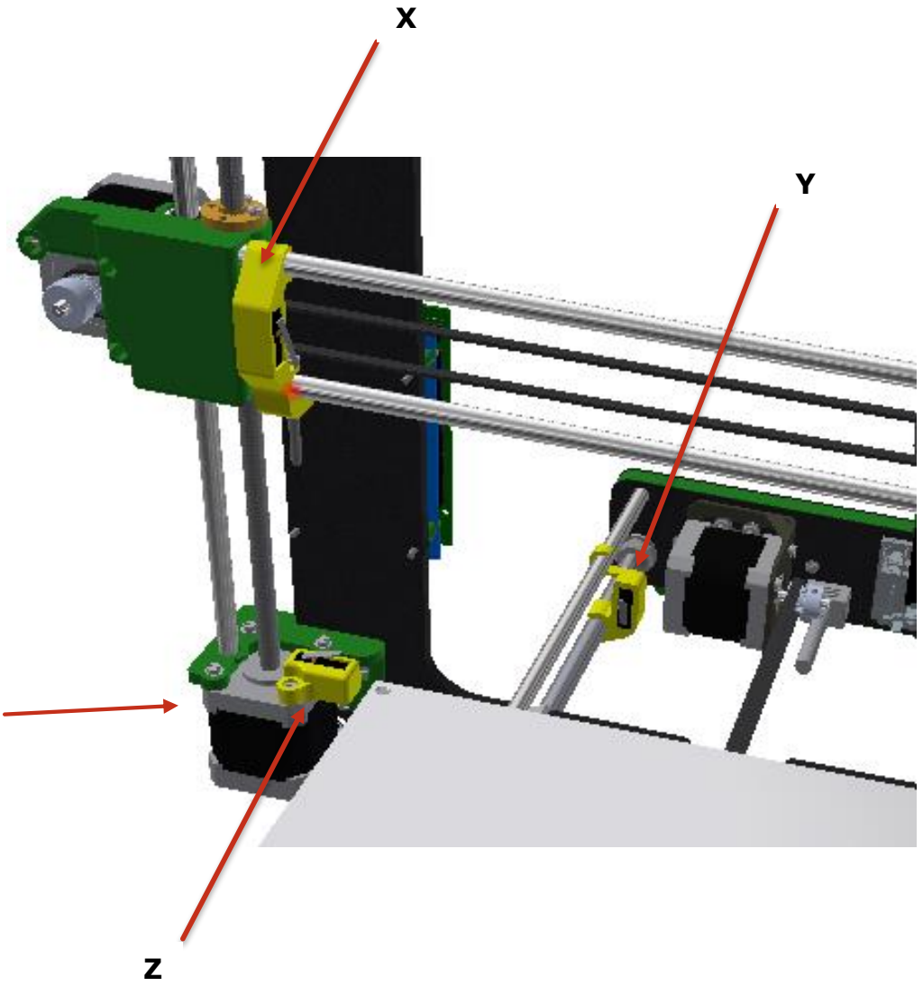
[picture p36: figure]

37

# [7] Endstops

Parts needed:

Printed X-Endstop holder | 1x
Printed X-Endstop holder | 1x
End switch | 2x
STEP 1

Time to attach your two end stops, one for each axis as seen in the image. First thing you need to do is insert the end switches into the printed parts. These press fit into place and have wires pre-soldered on. Make sure that you feed the connector and wire through the back of the holder before you press them down into place.

You will not need this
Z-Endstop due to your
inductive probe

38

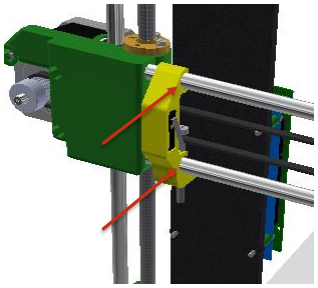
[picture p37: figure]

STEP 2
- Snap the x-axis end switch holder onto the two M8 smooth rods.
STEP 3
- Snap the y-axis end switch assembly to the M10 threaded rod. The top ‘hook’ keeps the mount vertical

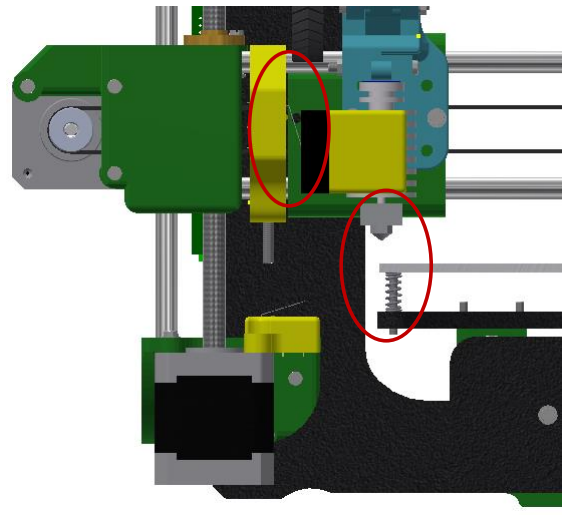
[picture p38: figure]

39

STEP 4

Now it’s time to position the two end switch assemblies. The point of this is to ensure the tip of the nozzle ‘homes’ to the front left corner of the bed.

- First up is the x-axis. Position the X end-switch assembly so that the tip of the nozzle lines up with the left edge of the print bed when the switch makes contact with the x-carriage.
- Next, the y-axis. The Y end switch assembly needs to be positioned so that the tip of the print nozzle lines up with the front edge of the print bed.

The switch actuates up against the edge of the plastic bearing holder.

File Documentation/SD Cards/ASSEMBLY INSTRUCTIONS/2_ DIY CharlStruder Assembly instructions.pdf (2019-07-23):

# DIYElectronics

## CharlStruder Assembly Instructions

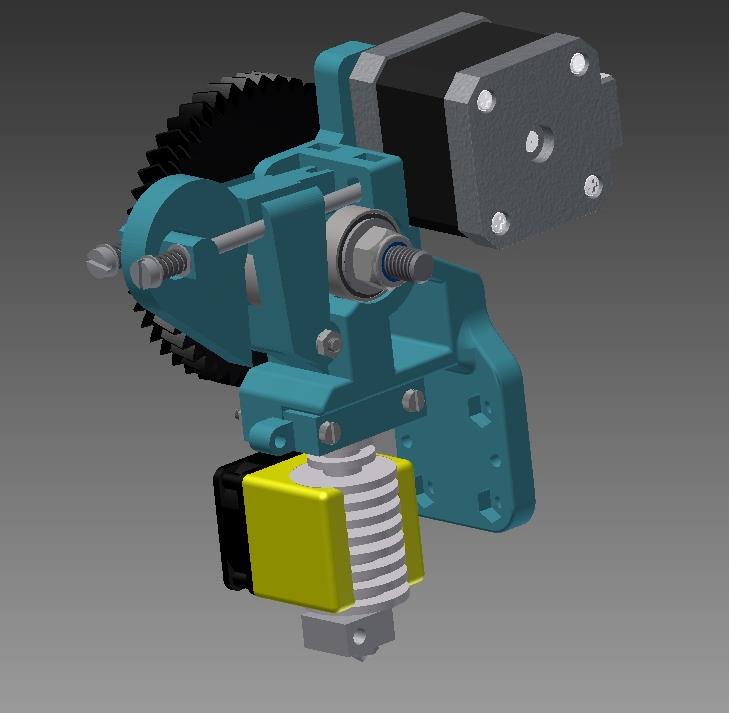
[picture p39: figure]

# Please refer to the last page for the full exploded diagram and component list!

Step 1

Components needed:

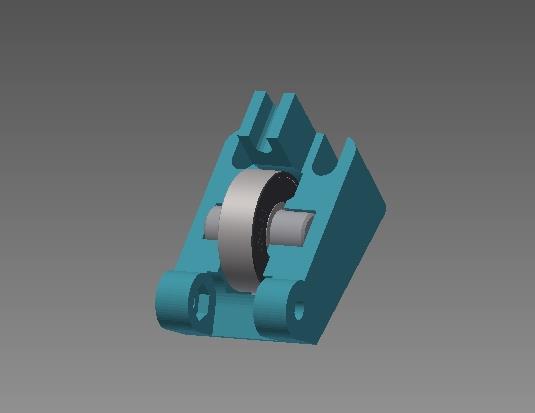
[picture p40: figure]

- Birdnose guidler
- M8x20mm idler axle
- 1x 608 bearing

Slide the 20mm idler axle through the 608 bearing and press fit into the slot of the birdnose guidler. This fit is quite tight and a mallet or vice might be needed to coax it in.

Make sure that the bearing spins with relative ease.

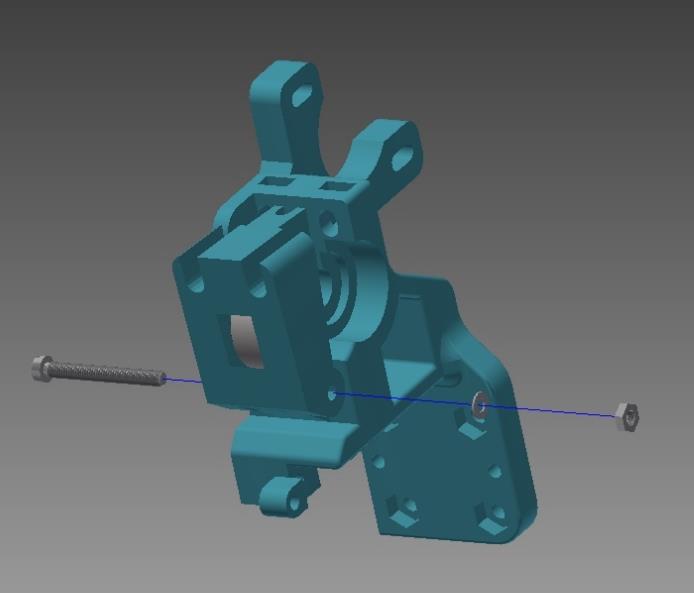
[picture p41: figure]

Step 2
- Extruder body
- 1x M3x30 machine screw
- 1x M3 washer
- 1x M3 nut

Connect the guilder assembly from above to the extruder body with an M3x30 machine screw and secure on the other end with an M3 washer and nut.

The guidler needs to be able to freely pivot.

Step 3
- 1x M8 hobbed bolt
- 1x big printed gear
- 2x 608 bearings
- M8 Washers
- 1x M8 nyloc nut

Slide the hobbed bolt through the big gear,
followed by about 4 to 6 washers and a 608
bearing.

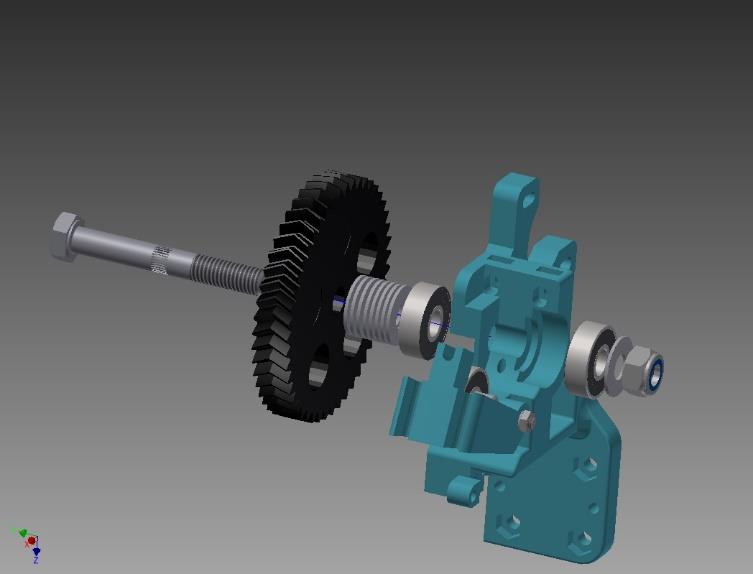
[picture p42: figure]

Slide this arrangement though the hole of the extruder body, where another bearing, single washer and M8 nyloc nut need to be placed on the hobbed bolt’s end. This order can be seen in the picture.

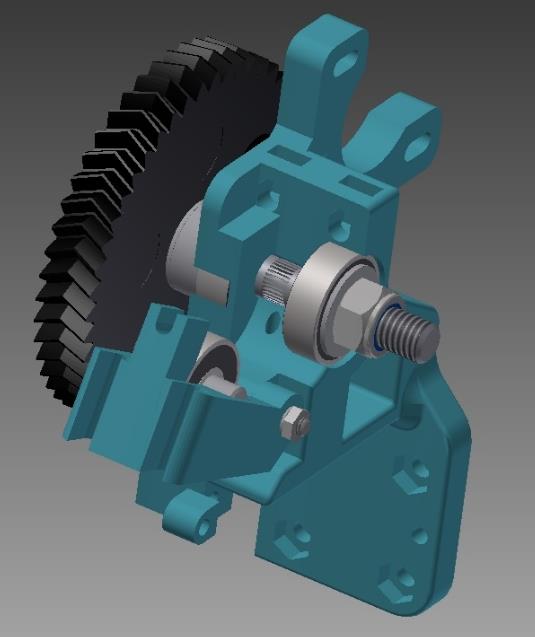
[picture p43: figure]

Tighten the nyloc nut until both bearings are press-fit securely into their captive slots and until the gear rotates with relative ease.

NOTE: it is extremely important that that the hobbed part of the bolt is centred and aligned with the filament hole (as shown in the picture to the right). If this is not centred you will need to add or remove the washers in-between the gear and bearing until you get this right.

Step 4
- Nema17 stepper motor
- Small printer gear (pinion)
- 1x M3 grub screw
- 3x M3x12 machine screws
- 3x M3 washers
- 4x M3 nuts

First you need to drill out the centre of the printed pinion gear with an M5 drill bit.

Press fit an M3 captive nut into the base of the pinion gear far enough so that the M3
grub screw can screw into it.

Then press fit this pinion gear onto the

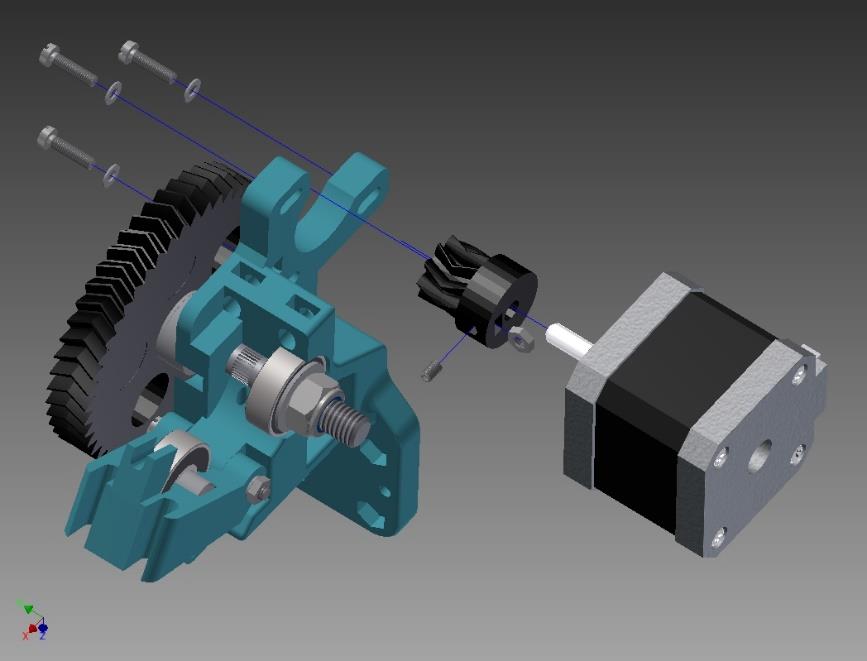
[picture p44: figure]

stepper motor shaft. Secure it with the M3 grub screw

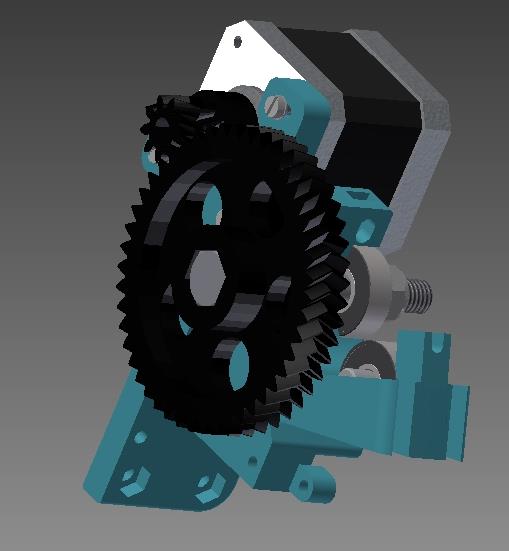
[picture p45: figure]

Secure the stepper motor to the body of the extruder using three M3x12 machine screws and washers as shown in the above picture.

Make sure that the teeth of the pinion and gear line up properly. You may need to adjust the pinion position on the motor shaft and the motor’s three M3 screws connecting it to the extruder body.

Once all of this is done your extruder should at this stage look like the image to the right.

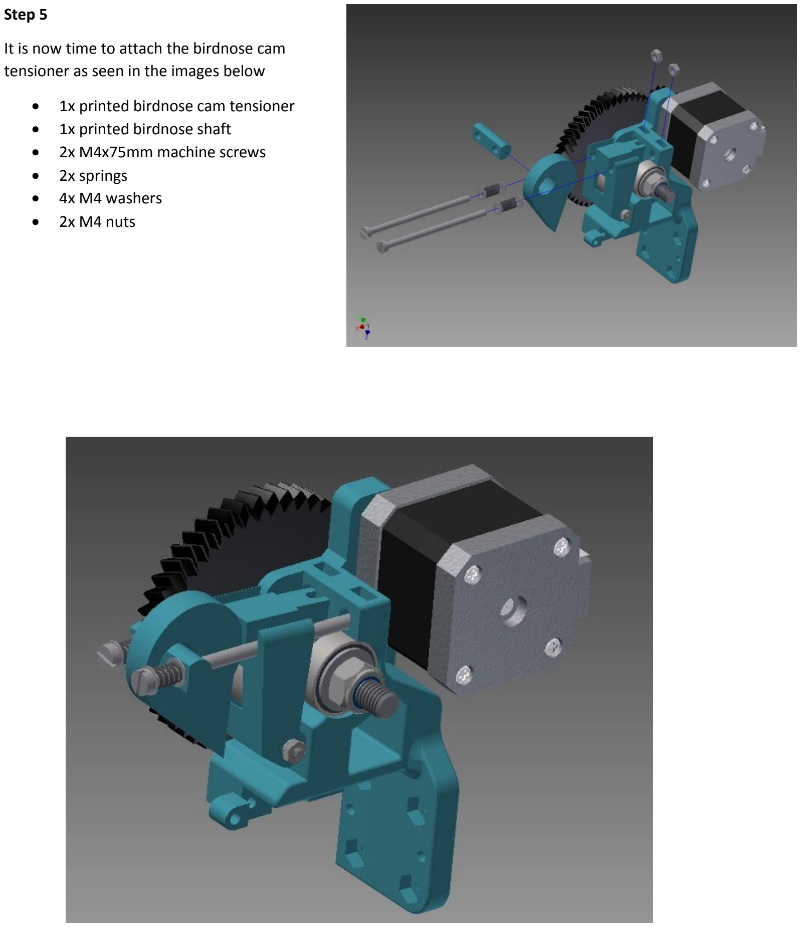
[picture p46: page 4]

Step 5

It is now time to attach the birdnose cam tensioner as seen in the images below

- 1x printed birdnose cam tensioner
- 1x printed birdnose shaft
- 2x M4x75mm machine screws
- 2x springs
- 4x M4 washers
- 2x M4 nuts

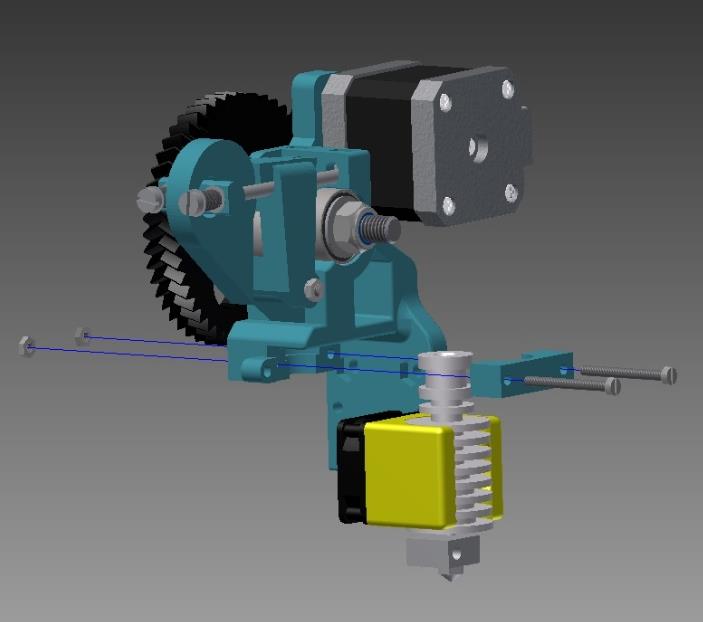
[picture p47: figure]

Step 6
- Hot end assembly (All Metal or J-head)
- 1x printed hotend clamp
- 2x M3x30 machine screws
- 2x M3 nuts

Clamp the hot end into place using the printed clamp, machine screws and nuts. Fasten tightly.

Final Complete Assembly!

Now all you need to do is attach the extruder to the X-axis carriage via the 4 hole spaces on the main extruder block OR the 2 hole spaces depending which carriage you have.

Enjoy!!

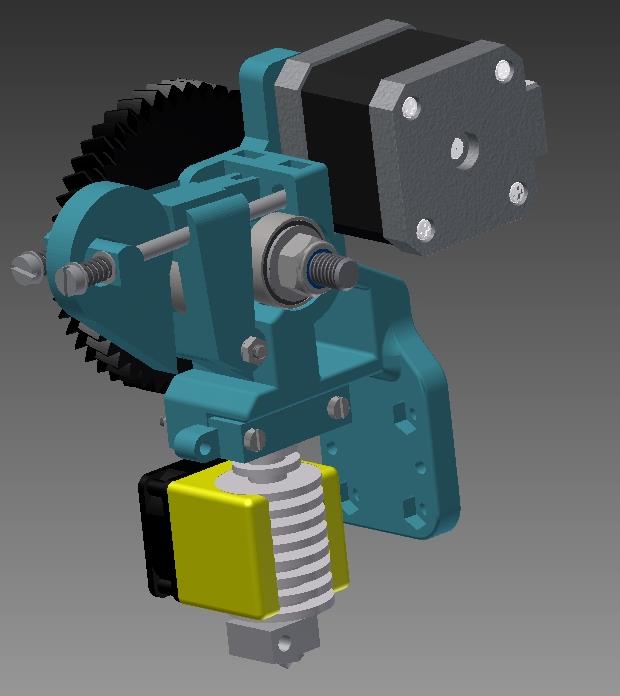
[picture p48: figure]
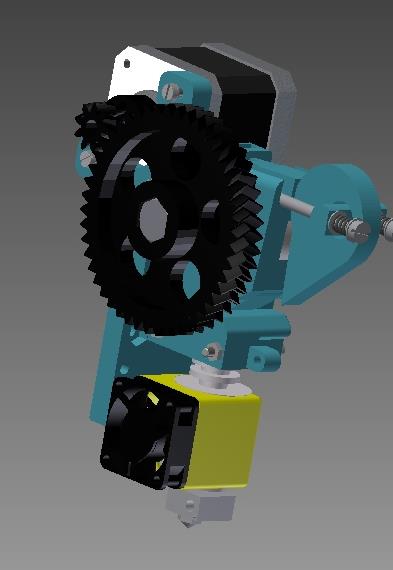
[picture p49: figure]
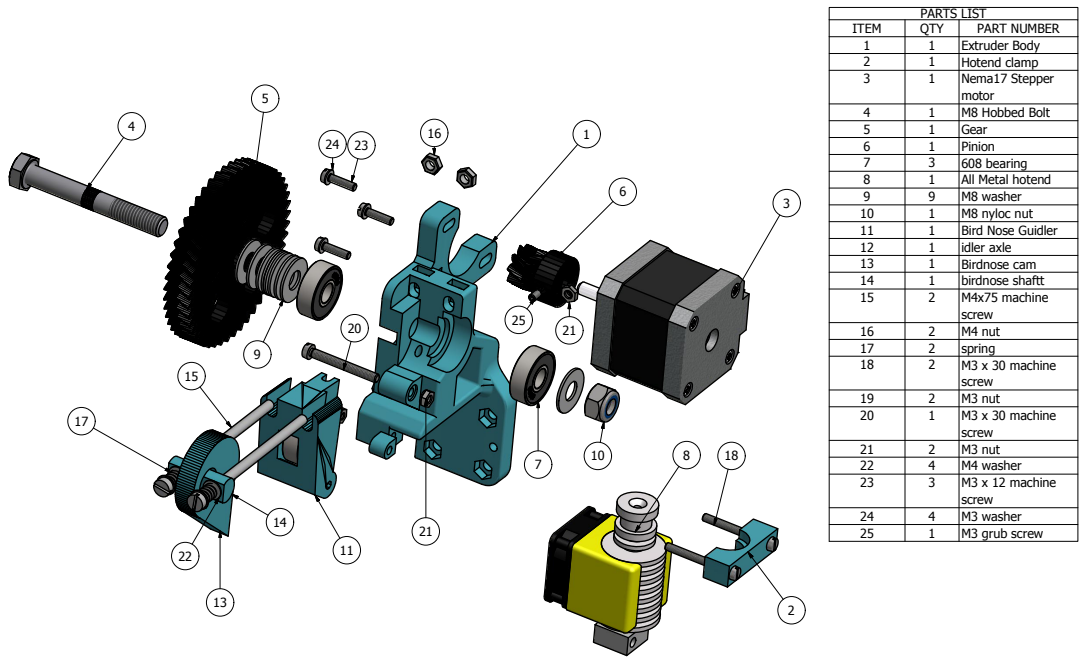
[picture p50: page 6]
cla; olt; All M; ylo; dle; xle

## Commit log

2019-07-22 Firmware files
    [Configuration.h]
2019-07-23 Firmware, STLs & Upgrade STLs
    semi mass upload of firmware files for all variants, printed parts for printers and upgrade stl's
    [608 Bearing Mount x8.stl, Autolevelmount.stl, Birdnose Guidler.stl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]
2019-07-23 SD card variants upload
    [Configuration.h, Configuration_adv.h]
2019-07-23 Folder rename
    [608 Bearing Mount x8.stl, Autolevelmount.stl, Birdnose Guidler.stl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]
2019-09-02 -Gcode
    removed presliced gcodes
    [DIY_PSU_Cover.stl, E3D_V6_40mm_Fan_v2.stl, Fan Shroud V6 30mm.stl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]
2019-09-02 Updated SD Card dir
    +UBL script & readme
    [Configuration.h, Configuration_adv.h]
